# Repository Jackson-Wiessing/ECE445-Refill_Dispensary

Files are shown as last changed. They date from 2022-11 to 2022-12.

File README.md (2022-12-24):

# ECE445-Refill_Dispensary

**Welcome to our refill dispensary repo!**

**Introduction:** 

Plastic waste is a massive issue world-wide, particularly as it pertains to the packaging of food and other household goods. The United States Environmental Protection Agency estimates that in 2018, 14 million tons of plastic was consumed for packaging in the USA with about seventy percent of that ending up in landfills[1]. Plastic waste is detrimental to the environment as it doesn’t decompose naturally on human time scales. End-user plastic waste is often unnecessary as consumers own containers capable of being reused. 

We built a vending machine that dispenses precise quantities of goods (between 10 g and 5 kg) into reusable containers. The goal of the machine is to get users to keep bringing the same container back. In addition to plastic waste, our machine tackles the issue of waste in general as users are no longer forced to get quantities larger than desired. 

 

**High-level requirements:**
1. The user is able to choose an item and quantity to get dispensed via buttons and rotary potentiometers. Before placing the order, the user will have some indication of the amount ordered within a tolerance of 10 grams for weights between .1 kg and 2kg.
2. The machine dispenses two different types of low-viscosity liquids and is able to perform 2 orders in succession. 
3. The machine can deliver another order properly after 1 of the liquids is switched out or refilled. 

**Block Diagram:** 



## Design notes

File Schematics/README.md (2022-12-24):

The easiest way to view our schematic and PCB layout is to download KiCad from https://www.kicad.org/download/. 
Once KiCad is downloaded, you'll need to clone this repo on your local machine.

To see the schematic open 1608_refill.kicad_sch.   

  

To see the PCB layout open 1608_refill.kicad_pcb.   



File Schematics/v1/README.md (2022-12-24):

This was our original schematic and PCB layout design. 

Schematic:    



PCB Layout:  



This PCB wasn't great as the components were close together which made it difficult to solder. Additionally, the resistor size that we were using were way too small and required the use of tweezers and a microscope to solder them onto the PCB. In our new design, we removed the screen from being on the PCB which gave us more room to spread parts out.

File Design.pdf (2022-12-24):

## 2 Design

## 2.1 Block Diagram

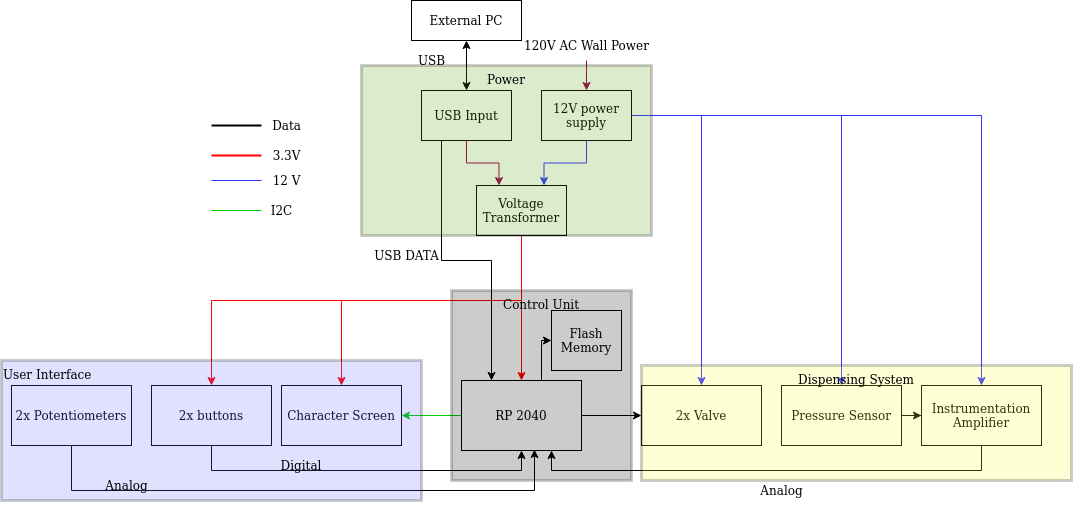
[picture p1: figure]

Figure 2: Block diagram for the vending machine

The block diagram has 4 main parts. The user interface interacts with the RP2040 by signaling button presses and potentiometer changes. The RP2040 then will display the number from the potentiometer onto the character screen of the user interface. The dispensing system valves are controlled by the RP2040. Additionally, the pressure sensor in the dispensing system will notify the RP2040 when to start and stop dispensing. The flash memory will be used to store program instructions and data about the containers. Finally, the power subsystem will supply all other subsystems with the proper power type.

## 2.2 Power

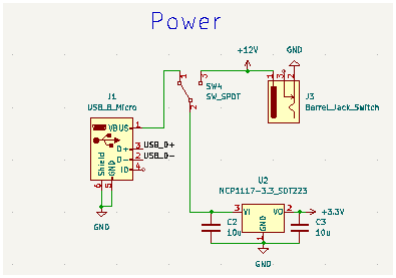
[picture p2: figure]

Figure 3: Power Subsystem

The power system consists of several parts: a barrel jack for the 12V line, a 3.3V voltage regulator, two 10uF capacitors, and a switch to be able to switch from the 5V USB power line to the 12V line from the barrel jack. The USB power input is necessary to initially flash the device, but the 12V input is intended as the main power input during normal usage. The high voltage components(e.g. solenoid valves) are only powered from the 12V line, but the digital components can be powered from either the USB or the 12V power supply filtered through the voltage regulator.

## 2.3 Dispensing System

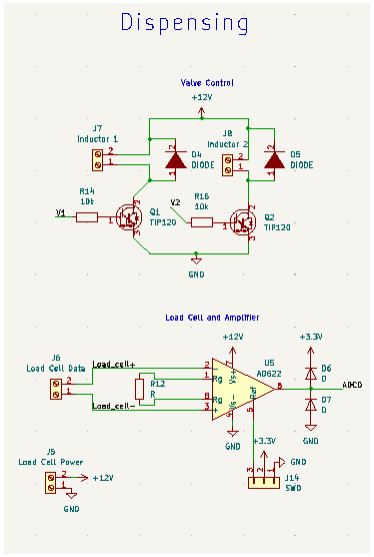
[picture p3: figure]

Figure 4: Dispensing Schematic

The dispensing system consists of two halves: solenoid valves and a load cell. The load cell is composed of a strain gauge (essentially a resistor whose value changes as it is bent) attached across a Wheatstone bridge. This generates a small differential voltage that is then fed through an instrumentation amplifier. The solenoid valves are simple 12V 400mA valves that are by default closed, each of which is connected to a Darlington BJT transistor and a flyback diode.

Originally, we planned to feed the load cell values through the AD622 instrumentation amplifier which would allow the value to be read by an ADC port of the microcontroller. We added in an analog to digital converter (ADC) protection circuit at the output of the amplifier to ensure we didn’t overload the ADC on the microcontroller as the instrumentation amplifier required 12V while the microcontroller could only handle 3.3 V. After unit testing this section of the design on the breadboard, it was clear that something was wrong and it wasn’t going to work. Instead, we came up with another way to get the load cell values over to the microcontroller.

Our new method involved using an HX711 amplifier which had the 24-bit ADC built in. We used a MicroPython HX711 library to tare the scale and analyze the values coming from it [2]. This allowed the 2^24 or roughly sixteen million unique values that the ADC was capable of differentiating. A further advantage was that we could power this amplifier from the 3.3V line. However, this amplifier complicated our design because it did not conform to a standard data transfer protocol. We were successfully able to read values from the load cell this way, however, it was too late to make a spot for the HX711 on the printed circuit board.

## 2.4 User Interface

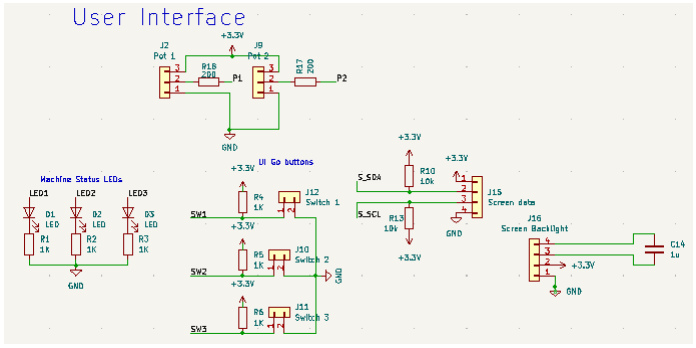
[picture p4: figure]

Figure 5: User Interface Schematic

The user interface consists of two potentiometers, three push-buttons, three LEDs and a screen. Two buttons are located underneath the bottles which lets the user know which button to press to dispense an item. The potentiometers are each located underneath the buttons to signify that turning it controls the amount to be dispensed for that particular bottle. As the potentiometers are turned the value gets sent to the microcontroller which sends the proper value to the screen to update the amount to be dispensed in grams. There is a red button in the middle of the user interface which resets the machine after a restocking takes place or overflow gets cleaned up. This button sends the machine back to the beginning where it’s waiting for a user to place an order. There are three LEDs on the side of the machine which indicate to the user if the machine is ready for an order (green), the machine is processing an order (orange), or if the machine needs maintenance (red).

Originally, we planned to use the NHD-C0220BIZ screen from Newhaven Display as we thought it would interface well with the I2C while consuming little power. Unfortunately, that was not the case. After carefully building out the circuit specified in the datasheet and turning on power, the screen would heat up immediately and no text could be displayed. We decided to switch out the screen for an OLED LCD Display Board Module I2C IIC SSD1306. This screen was easier to use as there were only 4 pins instead of 12 and the screen worked well with the Machine, SSD1306, and OLED libraries in MicroPython[3]. The screen communicates the amount to be dispensed to the user, live-time updates of the amount dispensed, the final amount dispensed, and if the machine needs maintenance.

## 2.5 Control Unit

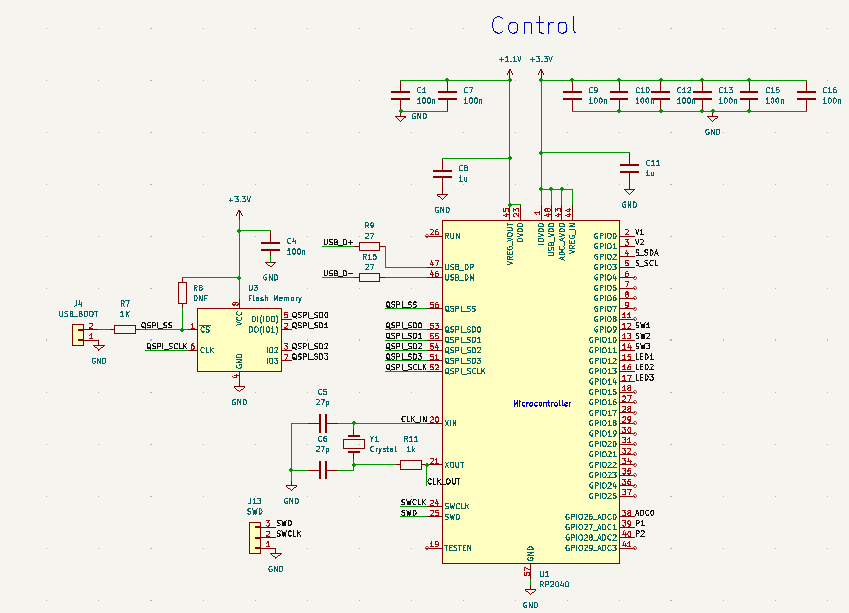
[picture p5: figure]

Figure 6: Control Unit Schematic

We used an RP2040 in combination with flash memory on the PCB. Our design is inspired by the one in the RP2040 Hardware design doc [4]. In order to load code to the RP2040, a USB connection was made to the computer, the code was downloaded and stored on the flash memory and then the program would continuously run. We chose the RP2040 as it was quite powerful for the price, which made it useful for scalability of the dispensing machines, and it is programmable using a variety of IDEs.
For testing purposes, we used a Raspberry Pi Pico on a breadboard which was cheap ($4), easily replaceable, and allowed us to test each subsystem before placing it on the PCB. Additionally, since the code relied on GPIO pins instead of physical pin numbers, we were able to interchange the code on the Pico for the RP2040 seamlessly.

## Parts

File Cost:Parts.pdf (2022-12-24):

14

# 4 Cost & Schedule

## 4.1 Cost Analysis

Description | Part | Manufacturer | Quantity | Extended Price | Link
Microcontroller | RP2040 | Raspberry Pi | 1 | $1.00 | Chicago Electronics (https://chicagodist.com/products/rp2040?src=raspberrypi)
I2C Screen | SSD1306 | AiTrip | 1 | $2.25 | Amazon (https://www.amazon.com/dp/B0B7RQ2RCF?psc=1&ref=ppx_yo2ov_dt_b_product_details)
Instrumentation amplifier/ADC | HX711 | AiTrip | 1 | $6.63 | Amazon (https://www.amazon.com/dp/B07SGPX7ZH?psc=1&ref=ppx_yo2ov_dt_b_product_details)
Red LED | HLMP3.301 -Red | Avago Technologies | 1 | $0.16 | ECE Supply Center (https://my.ece.illinois.edu/storeroom/catalog.asp)
Green LED | HLMP3507 -Green | Avago Technologies | 1 | $0.18 | ECE Supply Center (https://my.ece.illinois.edu/storeroom/catalog.asp)
Yellow LED | HLMP3401 -Yellow | Avago Technologies | 1 | $0.21 | ECE Supply Center (https://my.ece.illinois.edu/storeroom/catalog.asp)
Memory | IC FLASH 32MBIT SPI/QUAD 8SOIC | Winbond Electronics | 1 | $0.94 | Digi-Key (https://www.digikey.com/en/products/base-product/winbond-electronics/256/W25Q32/339733)
Barrel Jack | Breadboard-frien dly 2.1mm DC barrel jack | Adafruit | 1 | $0.95 | Adafruit (https://www.adafruit.com/product/373)
Micro USB Plug | Micro USB Plug Female | Adafruit | 1 | $0.95 | Adafruit (https://www.adafruit.com/product/1829)
Voltage Regulator | NCP1117 | OnSemi | 1 | $0.67 | DigiKey (https://www.digikey.com/en/products/detail/onsemi/NCP1117DT33T5G/921285)
Push Buttons | 0661273664773 | Cyclewet | 3 | $6.29 | Amazon (https://www.amazon.com/Cylewet-Momentary-Button-Switch-CYT1078/dp/B0752RMB7Q/ref=lp_5739464011_1_4)
Rotary Potentiometer | CA-WH148-10KB K | TWTADE | 2 | $10.99 | Amazon (https://www.amazon.com/TWTADE-Adjustable-Potentiometer-Resistance-XH2-54-3P/dp/B082FCRQS2)
Diode | IN4001 | ON Semiconductor | 4 | $1.50 | Adafruit (https://www.adafruit.com/product/755)
Transistor | TIP120 | Fairchild | 2 | $2.50 | Adafruit (https://www.adafruit.com/product/976)
100 nF Decoupling | 1C20Z5U103M0 | Sprague | 4 | $0.92 | ECE Supply (https://my.ece.illinois.edu/storeroom/catalog.asp)

15

Capacitor | 50B | | | | Center (https://my.ece.illinois.edu/storeroom/catalog.asp)
Solenoid | Plastic Water Solenoid Valve -12V - 1/2" Nominal | Adafruit | 2 | $13.90 | Adafruit (https://www.adafruit.com/product/997)
12V Power Supply | ALITOVE DC 12V 5A Power Supply Adapter | ALITOVE | 1 | $12.99 | Amazon (https://www.amazon.com/ALITOVE-Adapter-Converter-100-240V-5-5x2-1mm/dp/B01GEA8PQA)
Load Cell | 4541 | Adafruit | 1 | $3.95 | Adafruit (https://www.adafruit.com/product/4541#technical-details)
27 Ohm Resistor | CMP0805-FX-27 R0ELF | Bourns | 2 | $0.44 | Mouser (https://www.mouser.com/ProductDetail/Bourns/CMP0805-FX-27R0ELF)
1K Ohm Resistor | 810-MMZ1608R1 02ATD25 | TDK | 6 | $0.24 | Mouser (https://www.mouser.com/ProductDetail/Panasonic/ERJ-1RHD1001C?qs=I4vekKlxls8ZlmChpDSCCw%3D%3D)
10k Ohm Resistor | 603-RT0603DRE 1010KL | YAGEO | 2 | $0.24 | Mouser (https://www.mouser.com/ProductDetail/TE-Connectivity-Holsworthy/CRGCQ0603J10K)
27 pico Farad Capacitor | C0805X270J5GA C7800 | Kemet | 2 | $0.68 | Mouser (https://www.mouser.com/ProductDetail/KEMET/C0805X270J5GAC7800?qs=PqoDHHvF648EdaL1whdDkQ%3D%3D)
1uF Capacitor | 810-C1608X5R1 H105K | TDK | 2 | $0.14 | Mouser (https://www.mouser.com/ProductDetail/Taiyo-Yuden/TMR107B7105KA-T?qs=TuK3vfAjtkV9UZg3DkHnew%3D%3D)
10uF Capacitor | CL32Y106KCVZ NWE | Samsung | 2 | $2.24 | Mouser (https://www.mouser.com/ProductDetail/Samsung-Electro-Mechanics/CL32Y106KCVZNWE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)
100nF Capacitor | 810-C1608X7R1 H104K | TDK | 6 | $0.24 | Mouser (https://www.mouser.com/ProductDetail/TDK/C1005X7R1C104K050BC?qs=NRhsANhppD%252BhAGOapA8QKQ%3D%3D)
12MHz Oscillator | ABLS-12.000MH Z-B4-T | Abracon | 1 | $0.22 | Mouser (https://www.mouser.com/ProductDetail/ABRACON/ABLS-12.000MHZ-B4-T?qs=yTU0IcKoRlGSQ8ooxPPVnQ%3D%3D)
Total Cost | | | | $71.42

Table 5: Parts List

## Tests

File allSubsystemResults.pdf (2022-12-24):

## 3 Subsystem Results

Equation 1: Formula for calculating percent error

## 3.1 Power

Requirement: Power supply capable of generating 500mA on 3.3V line at +/- 0.2V Verification: While the machine is running, we will measure the voltage at the voltage transformer, as well as measuring the current drawn under load.
Results: The power supply worked as intended. We were able to measure a very consistent 3.289V on the 3.3V line. However, we were unable to test the current capacity on this line as it would have been difficult to break out a series connection from the voltage regulator.

Requirement: Power supply capable of generating 1A on 12V line at +/- 0.5V Verification: While the machine is running, we will measure the voltage at the voltage transformer, as well as measuring the current drawn under load.
Results: We were able to measure an appropriate voltage on the 12V line. However, again it would not have been feasible to measure the current as creating a series connection was difficult.
Line | Recorded Voltage
12V | 12.0995 V
12V to 3.3V | 3.28983 V
5V to 3.3V | 3.28974 V
Table 1: Voltage values for Power

## 3.2 Dispensing System

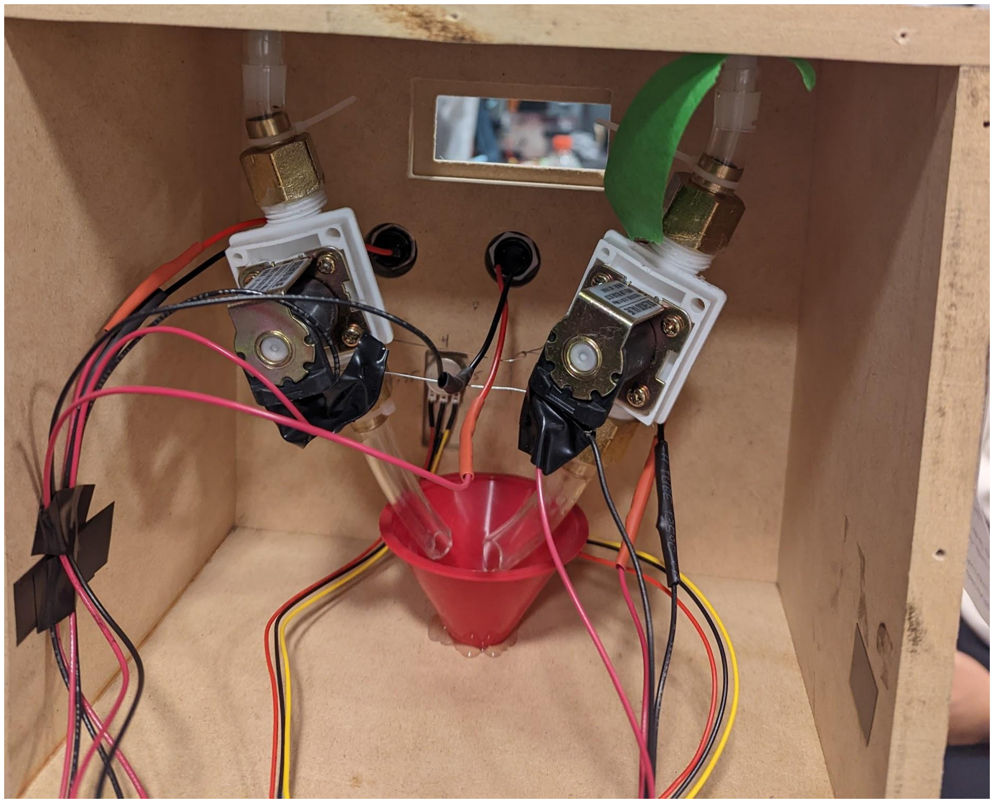
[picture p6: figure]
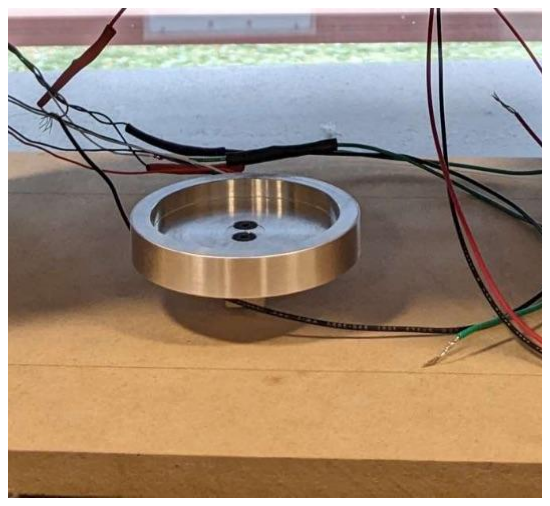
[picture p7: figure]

Figure 7: Solenoid Valves | Figure 8: Load Cell + Cup Holder

Requirement: The load cell should be able to weigh items with a tolerance of 10 g for weights up to 5 kg.
Verification: We weighed several objects on our load cell and compared the values to a scale.
Trial # | Experimental Weight | Actual Weight | Percent Error
1 | 15.63 g | 15.2 g | 2.83 %
2 | 200.75 g | 202.0 g | 0.619 %
Table 2: Load Cell Accuracy Trials

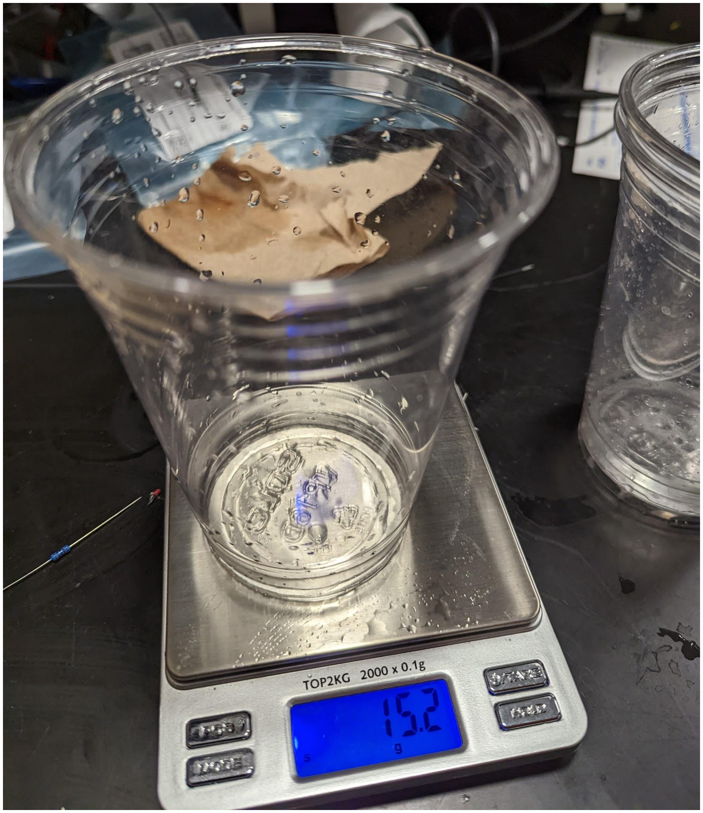
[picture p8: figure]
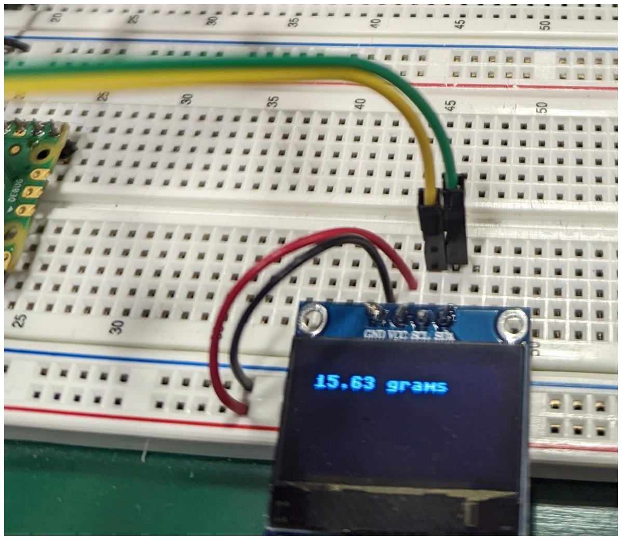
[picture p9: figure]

Figure 9: Trial 1 Experimental Results | Figure 10: Trial 1 Actual Results

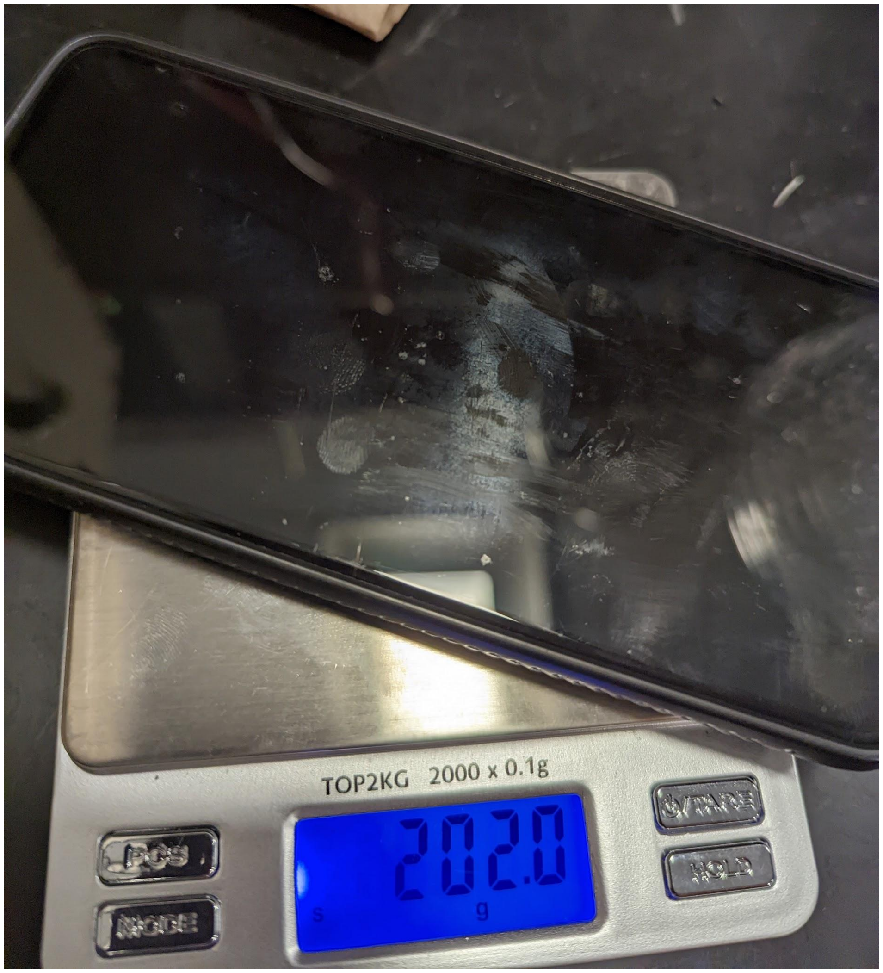
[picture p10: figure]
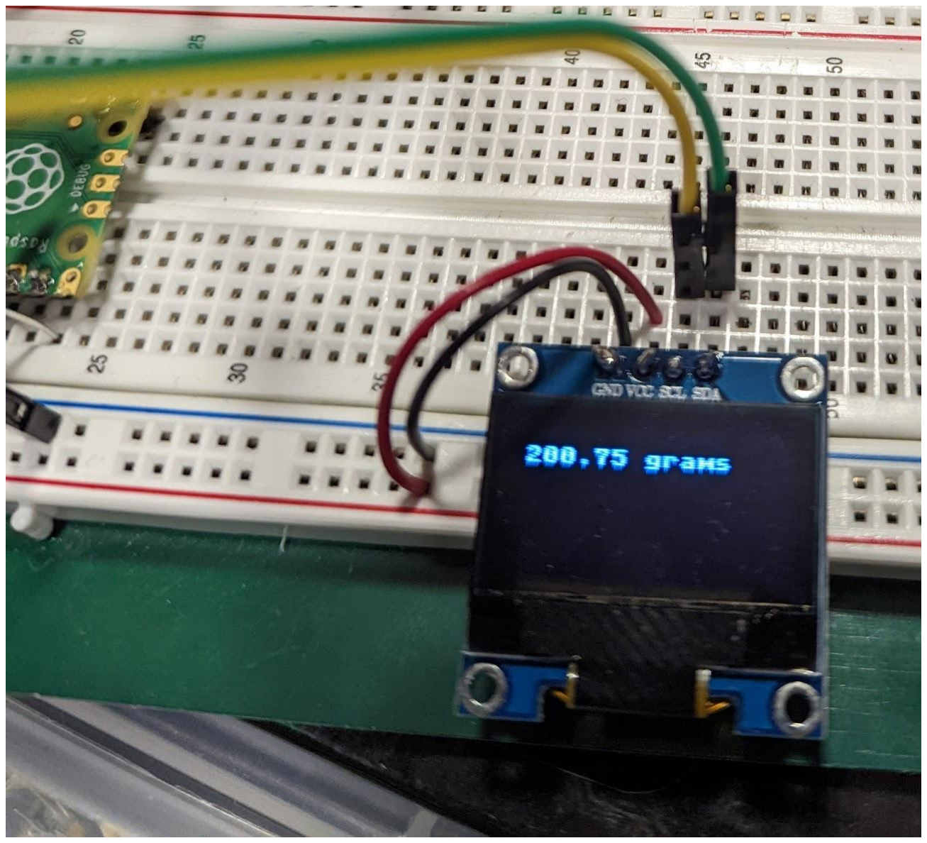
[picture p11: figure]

Figure 11: Trial 2 Experimental Results | Figure 12: Trial 2 Actual Results

Results: The load cell ended up being more precise than expected. The percent error ended up being very low.

Requirement: The value spun on the potentiometer is the amount that gets dispensed. Verification: We selected several small values on the potentiometer and then waited for the amount to get dispensed and weighed the results. The small weights are due to the slow flow rate of the machine.

Trial # | Amount Requested | Actual Weight | Percent Error
1 | 12 g | 13 g | 8.33 %
2 | 13 g | 15 g | 15.4 %
Table 3: Dispensing System Accuracy Trials

Results: The user ends up getting slightly more than what they requested. However, this is acceptable as it is advantageous to the customer.

Requirement: Voltage across inductor should always be less than the specified maximum voltage (12V) of the BJT
Verification: Measure the voltage across the inductor before and after closing the BJT switch.
Component | Recorded Voltage (V)
Solenoid 1 Diode | 11.158
Solenoid 2 Diode | 11.176

Solenoid 1 Screw Terminal | 11.318
Solenoid 2 Screw Terminal | 11.202
Table 4: Voltage across the inductors

Results: The drop across the inductor is 0V when it is turned off. When it is on the drop is under 12V.

## 3.3 Control System

Requirement: The microcontroller’s ADC should be precise enough to measure 250 unique values from the load cell.
Verification: To test this, we printed readings from the load cell with HX711 setup into the shell. We used our hands to apply variable force and watched the values go up. Results: The Pico was able to read 65,536 different values, which goes far above this requirement.

Requirement: Microcontroller sends proper signals to other subsystems. Verification: The correct text displays on the screen, the right item is chosen, machine status gets updated on the UI, and the proper item gets dispensed.
Results: As seen in the demo, we were able to dispense from both bottles by hitting the respective buttons and get results dispensed in the cup within the allowed tolerance. Additionally, the user saw the status LEDs change with the machine and screen text update throughout various parts of the process. Seeing the screen update can be seen in figures 9, 11, 13, and 14.

## 3.4 User Interface System

Requirement: The screen should use an I2C connection and be capable of displaying the item to be dispensed as well as its quantity with appropriate units.
Verification: Check that the correct text is displayed on the screen in 1 second after a button is pressed or a potentiometer is moved
Results: The screen displays different text for each state, as well as the amount selected and the amount dispensed, as seen in Figures 13 and 14. The screen is updated in real time as the amount selected and amount dispensed changes, with essentially no delay.

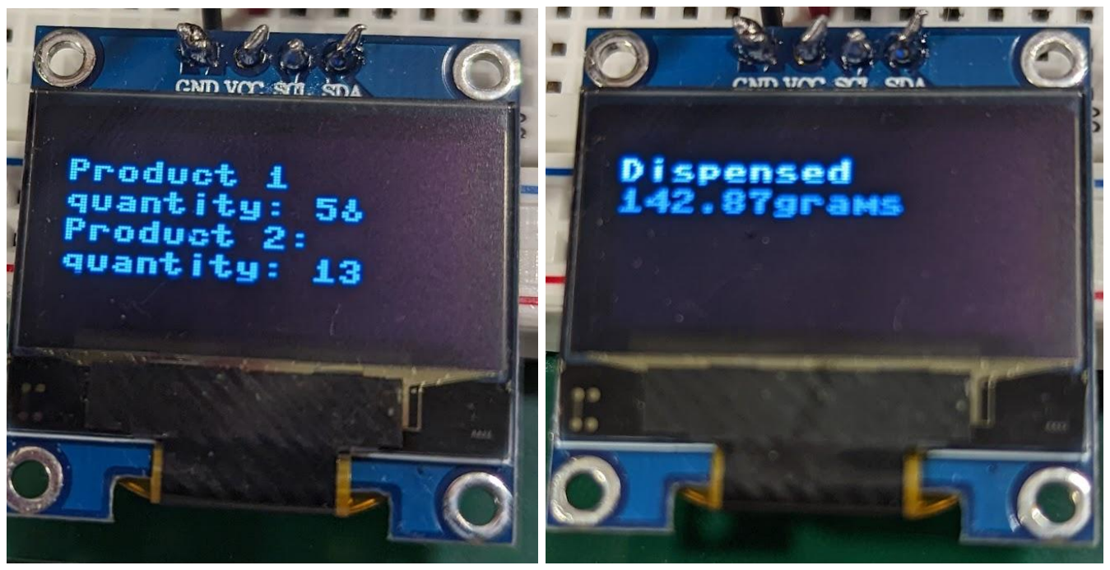
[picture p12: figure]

Figures 13 (left image) & 14 (right image): The left image shows the screen reflecting the potentiometer values during the selection state. The image on the right shows the actual quantity that got dispensed from an order.

Requirement: Status LEDS should match machine state within 1s of machine state changes.
Verification: Check the current machine state and see if the LED is the correct output. The amount of time required for the correct LED to turn on should be within 1 second of the state change.
Results: The LEDs changed almost instantaneously after a state change.

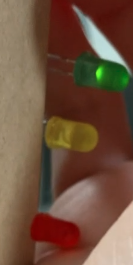
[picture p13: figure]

Figure 15: The Green LED is on - machine is ready for an order

Requirement: The machine should dispense the proper item.
Verification: Pressing a button will cause the machine to attempt to dispense the proper item.
Results: As seen in table 3 in section 3.2, after selecting 13 grams of a product to be dispensed, the machine dispensed 15 grams with a small amount of error.

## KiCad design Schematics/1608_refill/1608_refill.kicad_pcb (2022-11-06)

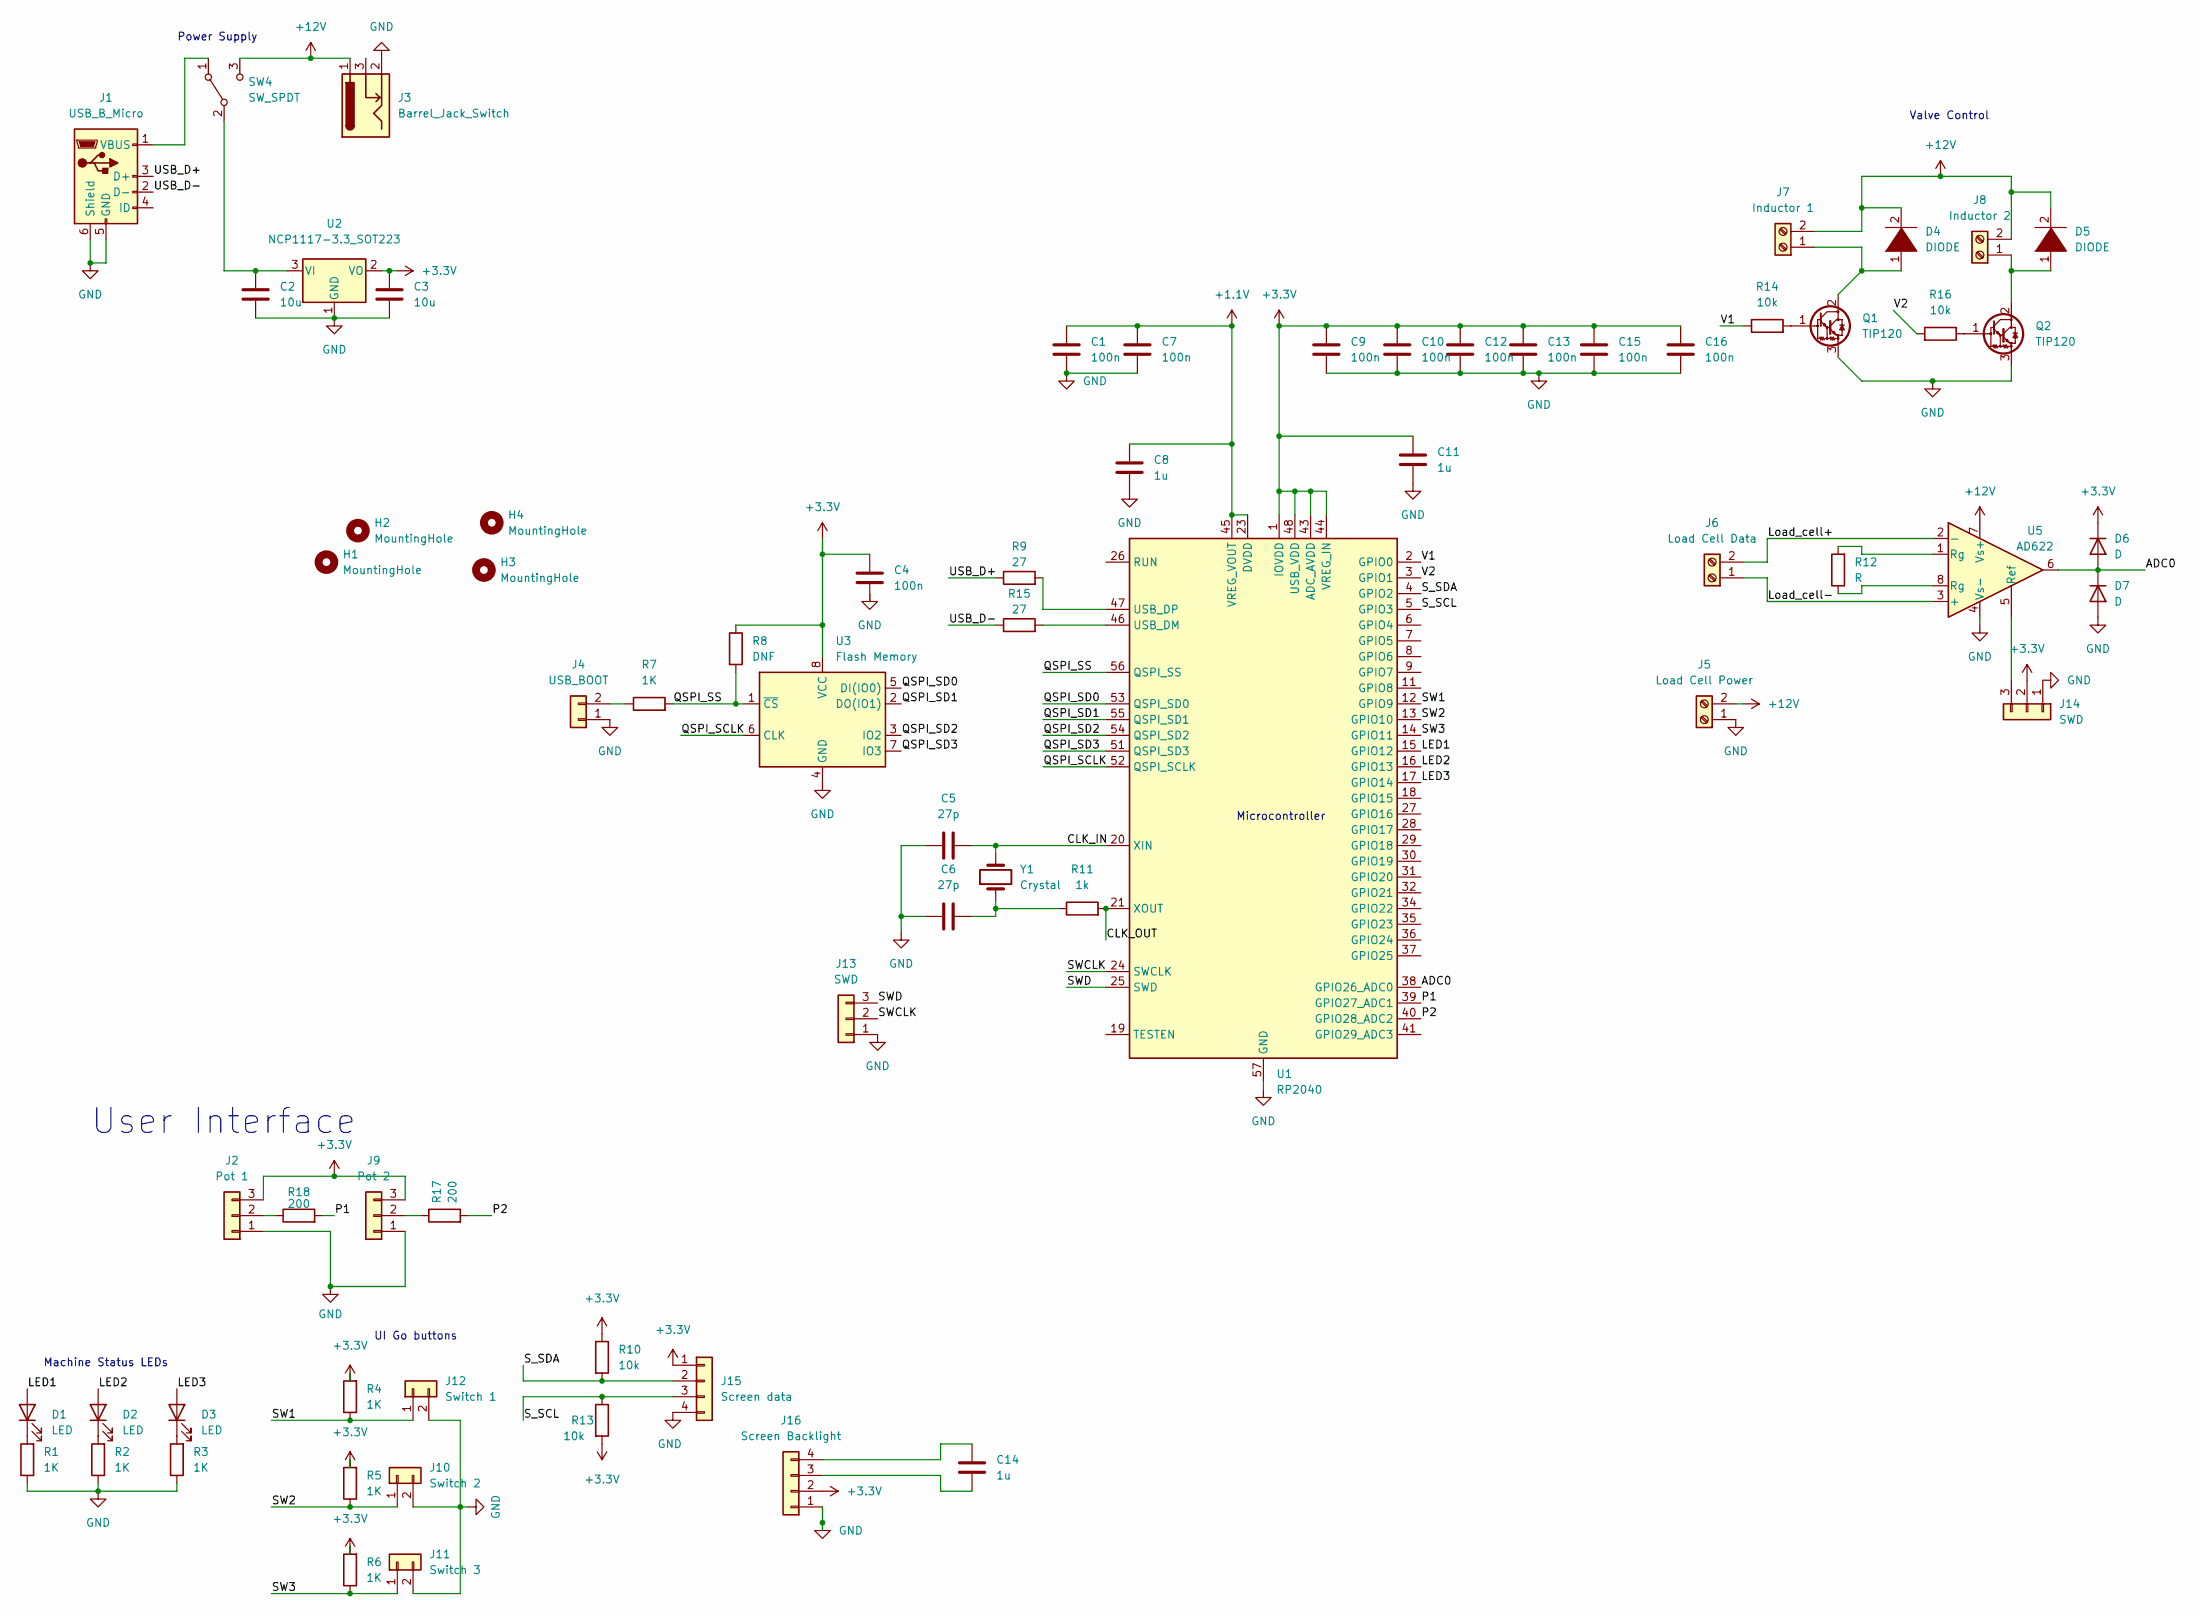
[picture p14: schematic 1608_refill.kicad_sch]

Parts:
C1, C4, C7, C9, C10, C12, C13, C15, C16: 100n; C_0603_1608Metric_Pad1.08x0.95mm_HandSolder
C2, C3: 10u; C_1210_3225Metric
C5, C6: 27p; C_0805_2012Metric
C8, C11, C14: 1u; C_0603_1608Metric_Pad1.08x0.95mm_HandSolder
D1, D2, D3: LED; LED_D3.0mm
D4, D5: DIODE; D_5W_P5.08mm_Vertical_AnodeUp
D6, D7: D; D_5W_P5.08mm_Vertical_AnodeUp
H1, H2, H3, H4: MountingHole; MountingHole_2.1mm
J1: USB_B_Micro; USB_Micro-AB_Molex_47590-0001
J2: Pot 1; JST_XH_B3B-XH-AM_1x03_P2.50mm_Vertical
J3: Barrel_Jack_Switch; BarrelJack_GCT_DCJ200-10-A_Horizontal
J4: USB_BOOT; JWT_A3963_1x02_P3.96mm_Vertical
J5: Load Cell Power; TerminalBlock_Altech_AK300-2_P5.00mm
J6: Load Cell Data; TerminalBlock_Altech_AK300-2_P5.00mm
J7: Inductor 1; TerminalBlock_Altech_AK300-2_P5.00mm
J8: Inductor 2; TerminalBlock_Altech_AK300-2_P5.00mm
J9: Pot 2; JST_XH_B3B-XH-AM_1x03_P2.50mm_Vertical
J10: Switch 2; JST_XH_B2B-XH-AM_1x02_P2.50mm_Vertical
J11: Switch 3; JST_XH_B2B-XH-AM_1x02_P2.50mm_Vertical
J12: Switch 1; JST_XH_B2B-XH-AM_1x02_P2.50mm_Vertical
J13, J14: SWD; JST_XH_B3B-XH-AM_1x03_P2.50mm_Vertical
J15: Screen data; JST_XH_B4B-XH-AM_1x04_P2.50mm_Vertical
J16: Screen Backlight; JST_XH_B4B-XH-AM_1x04_P2.50mm_Vertical
Q1, Q2: TIP120; TO-220-3_Vertical
R1, R2, R3, R4, R5, R6, R7: 1K; R_0603_1608Metric_Pad0.98x0.95mm_HandSolder
R8: DNF; R_0603_1608Metric_Pad0.98x0.95mm_HandSolder
R9, R15: 27; R_0805_2012Metric
R10, R13, R14, R16: 10k; R_0603_1608Metric_Pad0.98x0.95mm_HandSolder
R11: 1k; R_0603_1608Metric_Pad0.98x0.95mm_HandSolder
R12: R; R_Axial_DIN0204_L3.6mm_D1.6mm_P7.62mm_Horizontal
R17, R18: 200; R_0603_1608Metric_Pad0.98x0.95mm_HandSolder
SW4: SW_SPDT; SW_SPDT_CK-JS102011SAQN
U1: RP2040; QFN-56-1EP_7x7mm_P0.4mm_EP3.2x3.2mm
U2: NCP1117-3.3_SOT223; SOT-223-3_TabPin2
U3: Flash Memory; SOIC-8_5.23x5.23mm_P1.27mm
U5: AD622
Y1: Crystal; ABLS12MHZ

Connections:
+1V1: C1.1, C7.1, C8.1, U1.23 (DVDD), U1.45 (VREG_VOUT), U1.50 (DVDD)
+3.3V: C3.1, C4.1, C9.1, C10.1, C11.1, C12.1, C13.1, C15.1, C16.1, D6.1 (K), J2.3, J9.3, J14.2, J15.1, J16.2, R4.2, R5.2, R6.2, R8.1, R10.1, R13.2, U1.1 (IOVDD), U1.10 (IOVDD), U1.22 (IOVDD), U1.33 (IOVDD), U1.42 (IOVDD), U1.43 (ADC_AVDD), U1.44 (VREG_IN), U1.48 (USB_VDD), U1.49 (IOVDD), U2.2 (VO), U3.8 (VCC)
+12V: D4.2 (A), D5.2 (A), J3.1, J5.2, J7.2, J8.2, SW4.3 (C), U5.7 (Vs+)
/ADC0: D6.2 (A), D7.1 (K), U1.38 (GPIO26_ADC0), U5.6
/CLK_IN: C5.2, U1.20 (XIN), Y1.2
/CLK_OUT: R11.2, U1.21 (XOUT)
/LED1: D1.2 (A), U1.15 (GPIO12)
/LED2: D2.2 (A), U1.16 (GPIO13)
/LED3: D3.2 (A), U1.17 (GPIO14)
/Load_cell+: J6.2, U5.2 (-)
/Load_cell-: J6.1, U5.3 (+)
/P1: R18.2, U1.39 (GPIO27_ADC1)
/P2: R17.2, U1.40 (GPIO28_ADC2)
/QSPI_SCLK: U1.52 (QSPI_SCLK), U3.6 (CLK)
/QSPI_SD0: U1.53 (QSPI_SD0), U3.5 (DI(IO0))
/QSPI_SD1: U1.55 (QSPI_SD1), U3.2 (DO(IO1))
/QSPI_SD2: U1.54 (QSPI_SD2), U3.3 (IO2)
/QSPI_SD3: U1.51 (QSPI_SD3), U3.7 (IO3)
/QSPI_SS: R7.2, R8.2, U1.56 (QSPI_SS), U3.1 (~CS)
/SW1: J12.1, R4.1, U1.12 (GPIO9)
/SW2: J10.1, R5.1, U1.13 (GPIO10)
/SW3: J11.1, R6.1, U1.14 (GPIO11)
/SWCLK: J13.2, U1.24 (SWCLK)
/SWD: J13.3, U1.25 (SWD)
/S_SCL: J15.3, R13.1, U1.5 (GPIO3)
/S_SDA: J15.2, R10.2, U1.4 (GPIO2)
/USB_D+: J1.3 (D+), R9.1
/USB_D-: J1.2 (D-), R15.1
/V1: R14.1, U1.2 (GPIO0)
/V2: R16.2, U1.3 (GPIO1)
GND: C1.2, C2.2, C3.2, C4.2, C5.1, C6.1, C7.2, C8.2, C9.2, C10.2, C11.2, C12.2, C13.2, C15.2, C16.2, D7.2 (A), J1.5 (GND), J1.6 (Shield), J2.1, J3.2, J4.1, J5.1, J9.1, J10.2, J11.2, J12.2, J13.1, J14.1, J15.4, J16.1, Q1.3 (E), Q2.3 (E), R1.1, R2.1, R3.1, U1.57 (GND), U2.1 (GND), U3.4 (GND), U5.4 (Vs-)
unnamed: C2.1, SW4.2 (B), U2.3 (VI)
unnamed: C6.2, R11.1, Y1.1
unnamed: C14.1, J16.4
unnamed: C14.2, J16.3
unnamed: D1.1 (K), R1.2
unnamed: D2.1 (K), R2.2
unnamed: D3.1 (K), R3.2
unnamed: D4.1 (K), J7.1, Q1.2 (C)
unnamed: D5.1 (K), J8.1, Q2.2 (C)
unnamed: J1.1 (VBUS), SW4.1 (A)
unnamed: J2.2, R18.1
unnamed: J4.2, R7.1
unnamed: J9.2, R17.1
unnamed: J14.3, U5.5 (Ref)
unnamed: Q1.1 (B), R14.2
unnamed: Q2.1 (B), R16.1
unnamed: R9.2, U1.47 (USB_DP)
unnamed: R12.1, U5.8 (Rg)
unnamed: R12.2, U5.1 (Rg)
unnamed: R15.2, U1.46 (USB_DM)

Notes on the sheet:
Machine Status LEDs
Microcontroller
Power Supply
Valve Control
User Interface
UI Go buttons

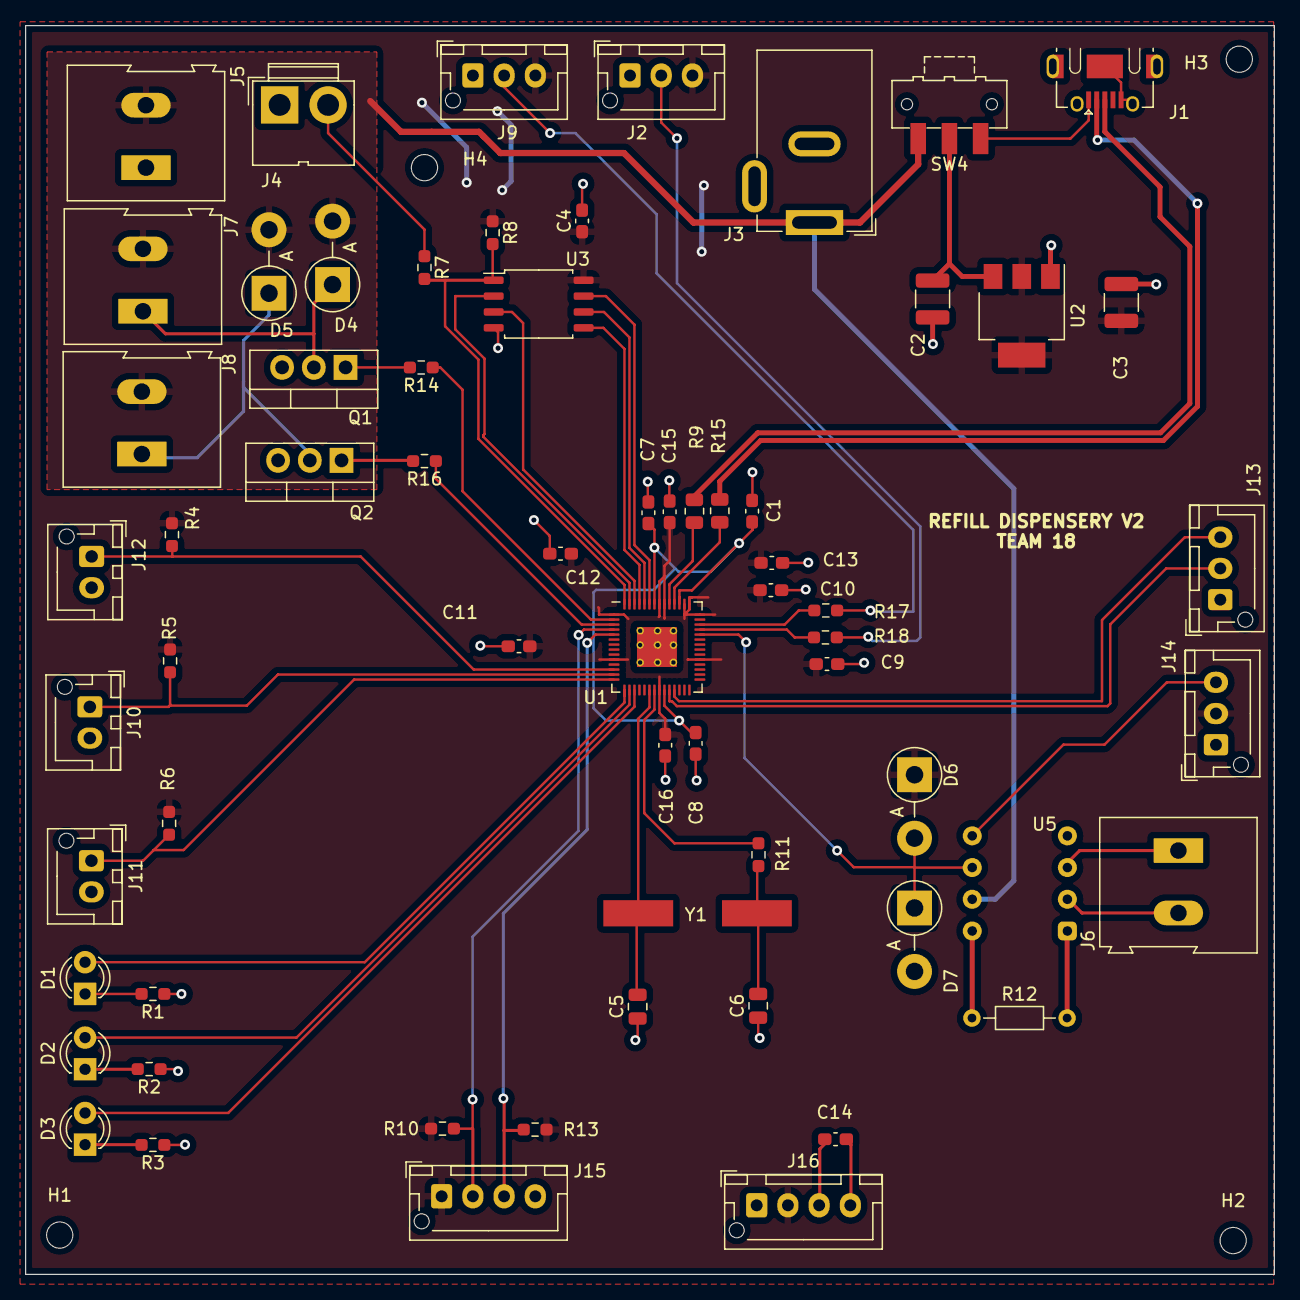
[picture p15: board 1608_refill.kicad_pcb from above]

Board: 2 copper layers, 100.0 x 100.0 mm, 69 parts (0 on the bottom side), 51 nets.

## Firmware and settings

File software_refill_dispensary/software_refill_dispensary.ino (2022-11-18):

#include <Wire.h>

/* Software for Refill Dispensary */
#define PRESSED 1 
#define SCREEN_ADDR 0x78
#define OVERFLOW -1
#define SUCCESS 0 
#define OUTOFSTOCK 1

/* UI components */
const int pot_1 = 32; // for user selection 1
const int pot_2 = 34; // for user selection 2

const int button_1 = 12; // for user selection 1
const int button_2 = 14; // for user selection 2
const int reset_button = 15; // resets the entire machine

const int green_led = 16; // machine status LEDs
const int yellow_led = 17;
const int red_led = 19;

/* Screen */
const int screen_data = 2; // data line for communicating between screen & microcontroller  -> was pin 4
const int screen_clock = 3; // was pin 5

/* Dispensing part */
const int load_cell = 31; // will send values to microcontroller
const int valve_1 = 1;
const int valve_2 = 2;

/* States can be categorized by the following:
Wait  - no buttons have been pressed
      - nothing is being dispensed
      - green status LED is on
      - screen value changes as potentiometers are turned
      - Conditions to check before entering the state: 
            1. button is pressed and the corresponding potentiometer has a non-zero value
            2. previous state was wait
            3. load cell reads a value > X grams -> we originally said 19 grams
Dispense  - machine status turns yellow
          - "zeros" out the scale
          - corresponding valve opens
          - updates the screen every few seconds
          - if the weight isn't changing after 10 seconds -> enter Debug mode bc something is out of stock 
          - if weight gets picked up -> immediately stop!
          - constantly checks if the load cell detects a weight within tolerance of requested quantity 
              ---> when it does, it stops & closes the valve
            - ensures that there's no overflow otherwise it will move into the debug state
Debug - machine status is red
      - all button presses and potentiometer spins get ignored until the reset button is hit
*/
enum State {Wait, Dispense, Debug};

/* Tracks the current state of the machine */
State curState;

/* Screen will be updating periodically to keep the user informed
Normal - Selected Product X, Quantity = Y
NoContainer - Error: Must Place Container!
NoQuantity - Error: Must Select Quantity!
*/
enum ScreenText {Normal, NoContainer, NoQuantity};
ScreenText curText;

/* Initialize all UI components to off or 0 */
int button_1_state, button_2_state, reset_state, pot_1_state, pot_2_state = 0; 

/* Keeps track of the weight to dispense */
int weight = 0; 

/* TESTING - The goal of this function is to let us know if we're properly understanding how the buttons work */
void readButtons(int * buf){
  int but_1_state = digitalRead(button_1);
  int but_2_state = digitalRead(button_2);
  int res_state =  digitalRead(reset_button);
  
  if (but_1_state == 1){
      Serial.println("button 1 pressed");
  }
  if (but_2_state == 1){
      Serial.println("button 2 pressed");
  }
  if (res_state == 1){
    Serial.println("reset pressed");
  }
}

/* TESTING - The goal of this function is to figure out the values given by potentiometer readings */
void readPots() {
  int p_1_state = analogRead(pot_1);
  int p_2_state = analogRead(pot_2);
  Serial.println("Pot 1 Value: ");
  Serial.println(p_1_state);
  Serial.println("Pot 2 Value: ");
  Serial.println(p_2_state);
}

/* TESTING - Testing for the first part of the pseudocode */
void doButtonsAndPotsWork() {
  int but_1_state = digitalRead(button_1);
  int but_2_state = digitalRead(button_2);
  int p_1_state = analogRead(pot_1);
  int p_2_state = analogRead(pot_2);

  if (but_1_state == PRESSED && p_1_state > 0) {
    Serial.println("Pot 1 Value: ");
    Serial.println(p_1_state);
    digitalWrite(LED_BUILTIN, HIGH);
  }
  else if (but_2_state == PRESSED && p_2_state > 0) {
    Serial.println("Pot 2 Value: ");
    Serial.println(p_2_state);
    digitalWrite(LED_BUILTIN, HIGH);
  }

  delay(100);
  digitalWrite(LED_BUILTIN, LOW);
}

/* Updates the status of the leds */
void updateLEDS(int green_status, int yellow_status, int red_status){
  digitalWrite(green_led, green_status);
  digitalWrite(yellow_led, yellow_status);
  digitalWrite(red_led, red_status);
}

/* Setsup screen to write to */
void setupScreen() { // recheck the pins for SDA or SCL
/*
  Wire.setSDA(screen_data); // the 3 of these were previously Wire1
  Wire.setSCL(screen_clock);
  Wire.begin(SCREEN_ADDR); 
  */
}

/* Gets the status of the buttons & potentiometers */
void readUI() {
  button_1_state = digitalRead(button_1);
  button_2_state = digitalRead(button_2);
  pot_1_state = analogRead(pot_1);
  pot_2_state = analogRead(pot_2);
  reset_state = analogRead(reset_button);
}

// enum ScreenText {Normal, NoContainer, NoQuantity};
/* */
void updateScreen(ScreenText text) {
  switch (text) {
    case Normal:
      // Selected Product X, Quantity = Y 
      break;
      
    case NoContainer: 
      // Error: Must Place Container!
      break;

    case NoQuantity:
      // Error: Must Select Quantity! 
      break;
      
    default:
      break;    
  }
}

/* opens the respective valve */
void openValve(int v) {
  digitalWrite(v, HIGH);
}

/* closes both valves */
void closeValves() {
  digitalWrite(valve_1,LOW); //ensure that valves are closed
  digitalWrite(valve_2,LOW);
}

/* this function is called as soon as a valve opens. It constantly checks the weight of the container with the weight of the load cell */
int fillUp() {
  int count = 0;
  int prev_value = -1;
  int load_cell_val = 0; // get the value of the load cell here

  while (load_cell_val < (.9 * weight)) {
    if (count == 10) {
      return OUTOFSTOCK;    
    }
    
    if (prev_value == load_cell_val) {
      count ++;
    }
    delay (10);
    prev_value = load_cell_val;
  }

  if (load_cell_val > (1.1 * weight)) {
    return OVERFLOW;
  }
  else {
    return SUCCESS;
  }
  
}

/* Runs once at the beginning */
void setup() {
  pinMode(pot_1, INPUT);
  pinMode(pot_2, INPUT);

  pinMode(button_1, INPUT);
  pinMode(button_2, INPUT);
  pinMode(reset_button, INPUT);

  pinMode(green_led, OUTPUT);
  pinMode(yellow_led, OUTPUT);
  pinMode(red_led, OUTPUT);

  pinMode(screen_data, OUTPUT);
  pinMode(screen_clock, OUTPUT);

  pinMode(load_cell, INPUT);
  pinMode(valve_1, OUTPUT);
  pinMode(valve_2, OUTPUT);

  pinMode(LED_BUILTIN, OUTPUT);

  Serial.begin(9600); // starts communication through the USB connection at a baud rate of 9600
  setupScreen();
}

int res; 
/* Constantly runs */
void loop() {
  if (reset_state == PRESSED) {
    closeValves();
    curState = Wait;
  }
  switch (curState) { //enum State {Wait, Start, Dispense, End, Debug};
    case Wait:
      // closeValves(); // idk if we want this here...
      updateLEDS(1,0,0); // green
      readUI(); 
      if (button_1_state == PRESSED && pot_1_state > 3) {
        curState = Dispense;
        weight = pot_1_state;
        openValve(valve_1);
      }
      else if (button_2_state == PRESSED && pot_2_state > 3) {
        curState = Dispense;
        weight = pot_2_state;
        openValve(valve_2);
      }
      break;
    
    case Dispense:
      updateLEDS(0,1,0);  // yellow
      res = fillUp();
      if (res == OVERFLOW || res == OUTOFSTOCK) {
        curState = Debug;
      }
      else {
        curState = Wait;
      }
      closeValves();
      break;

    case Debug:
      updateLEDS(0,0,1); // red
      // write to screen some error message
      if (reset_state == PRESSED) {
        curState = Wait;
      }
      weight = 0;
      closeValves();
      break;
    
    default:
      break;
  }
}

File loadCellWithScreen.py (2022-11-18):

from machine import Pin, I2C
from ssd1306 import SSD1306_I2C
from oled import Write, GFX, SSD1306_I2C
from oled.fonts import ubuntu_mono_15, ubuntu_mono_20
import utime
from hx711 import HX711
from utime import sleep_us
from time import sleep


WIDTH =128

HEIGHT= 64

i2c = I2C(0, scl = Pin(1), sda = Pin(0), freq=200000)

 #print("i2c initialization done")

oled = SSD1306_I2C(WIDTH, HEIGHT, i2c)

#print("post line 22")

def display_weight(weight):
    oled.fill(0)
    write15 = Write(oled, ubuntu_mono_15)

    write20 = Write(oled, ubuntu_mono_20)

    write15.text("Weight is", 0, 10)

    oled.text(str(int(weight)), 5, 35)
    oled.text("grams", 60, 35)

    oled.show()

def display_calculating():
    oled.fill(0)
    oled.text("Calculating", 10, 35)
    oled.show()


def remove_outliers():
        print("entered remove outliers")
        vals = [-10, -10, -10, -10, -10, -10, -10]
        
        # 1. Get 7 readings from stable values
        print("getting readings")
        for i in range(len(vals)):
            print("reading in # ", i)
            reading = -10
            while reading < 0:
                reading = scales.stable_value()
                print(reading)
            vals[i] = reading
            
        # 2. check for outliers
        print("checking for outliers")
        vals.sort()
        print("vals: ", vals)
        median = vals[3]
        upper_fence = median + 1000
        lower_fence = median - 1000


        outlier_idx = []
        for i in range(len(vals)):
            if i > upper_fence or i < lower_fence:
                outlier_idx.append(i)
    
        print("outliers are at indices: ", outlier_idx)
        
        for i in outlier_idx:
            r = scales.stable_value()
            while (r < lower_fence or r > upper_fence):
                r = scales.stable_value()
            vals[i] = r
        
        average = 0
        for i in vals:
            average += i
            
        if (average == 0):
            return 0
        
        return average / 7
    
def scale_values():
    # TODO:
    # my phone is 227.8 grams
    display_calculating()
    res = remove_outliers()
    print("res = ", res)
    print("scaled value: ", res / 7.6997)
    return res / 7.6997
    


class Scales(HX711):
    def __init__(self, d_out, pd_sck):
        super(Scales, self).__init__(d_out, pd_sck)
        self.offset = 0

    def reset(self):
        self.power_off()
        self.power_on()

    def tare(self):
        self.offset = self.read()

    def raw_value(self):
        return self.read() - self.offset

    def stable_value(self, reads=10, delay_us=500):
        values = []
        for _ in range(reads):
            values.append(self.raw_value())
            sleep_us(delay_us)
        return self._stabilizer(values)

    @staticmethod
    def _stabilizer(values, deviation=10):
        weights = []
        for prev in values:
            if prev == 0:
                weights.append(0)
            else:
                weights.append(sum([1 for current in values if abs(prev - current) / (prev / 100) <= deviation]))
        return sorted(zip(values, weights), key=lambda x: x[1]).pop()[0]
    
                    

if __name__ == "__main__":
    scales = Scales(d_out=5, pd_sck=6)
    scales.tare()
    #while True:
        #val = scales.stable_value()
       # print(val)
      # res = remove_outliers()
       #print(res)
    while True:
        print(scales.stable_value())
        sleep(2)
    weight = scale_values()
    print(weight)
    
    display_weight(weight)
    #scales.power_off()

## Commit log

2022-09-19 Initial Schematic Drawing
    [Refill_Dispensary.kicad_pcb, Refill_Dispensary.kicad_sch]
2022-09-19 Schematic Outline
2022-09-24 Schematic mostly done
    [jtw6_miniencabulator.kicad_sch]
2022-09-26 minor changes
    [Refill_Dispensary.kicad_sch]
2022-10-08 everything is pretty
    [Refill_Dispensary.kicad_pcb]
2022-10-09 I'm cant make a PCB
    [Refill_Dispensary.kicad_pcb, Refill_Dispensary.kicad_sch, jtw6_miniencabulator.kicad_sch]
2022-10-10 I'm cant make a PCB again
    [Refill_Dispensary.kicad_pcb]
2022-10-10 board mostly finished
    [Refill_Dispensary.kicad_pcb, Refill_Dispensary.kicad_sch]
2022-10-10 update screen schematic
    [Refill_Dispensary.kicad_pcb]
2022-10-11 board v1
    [Refill_Dispensary.kicad_pcb, Refill_Dispensary.kicad_sch]
2022-10-11 board v1.1
    [Refill_Dispensary.kicad_sch]
2022-10-18 starting the software
    [Refill_Dispensary-B_Cu.gbr, Refill_Dispensary-B_Mask.gbr, Refill_Dispensary-B_Paste.gbr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]
2022-10-22 main arduino code added
2022-10-30 early 1608 upgrade sketches
    [1608_refill.kicad_pcb, 1608_refill.kicad_sch]
2022-10-30 gearing up for PCB 2
    [1608_refill.kicad_pcb, 1608_refill.kicad_sch]
2022-11-05 1608:all routes connected
    [1608_refill.kicad_pcb, 1608_refill.kicad_sch, Refill_Dispensary.kicad_pcb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]
2022-11-06 1608 mostly done
    [1608_refill.kicad_pcb, 1608_refill.kicad_sch]
2022-11-17 The load cell works within the tolerance!
    [loadCell.py]
2022-11-26 fixed pico main loop, now uses gpio pin initialization
    [refill micropython.py]
